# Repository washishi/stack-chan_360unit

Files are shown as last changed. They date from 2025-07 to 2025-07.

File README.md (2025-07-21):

# stack-chan_360unit
Rotation unit for Takao's SCS0009 version stack chan

## 説明
-  タカヲ([@mongonta555](https://x.com/mongonta555))さんの [SCS0009サーボ専用 ｽﾀｯｸﾁｬﾝ](https://raspberrypi.mongonta.com/about-products-stackchan-m5gobottom-version/) を回転させてもUSBケーブルが邪魔にならないようにするユニットです
- [【SCS0009専用】ｽﾀｯｸﾁｬﾝ タカオ版 ケースセット](https://mongonta.booth.pm/items/5186064)に後付けできます
-  M5Coreへの電源供給は Groveポート経由、USBコネクタ経由(外部/内部)いずれかで行うことができます  
-  USBコネクタ(外部/内部)を利用した場合は電源の供給だけでなくデータ通信も行うことができます
  
<br>
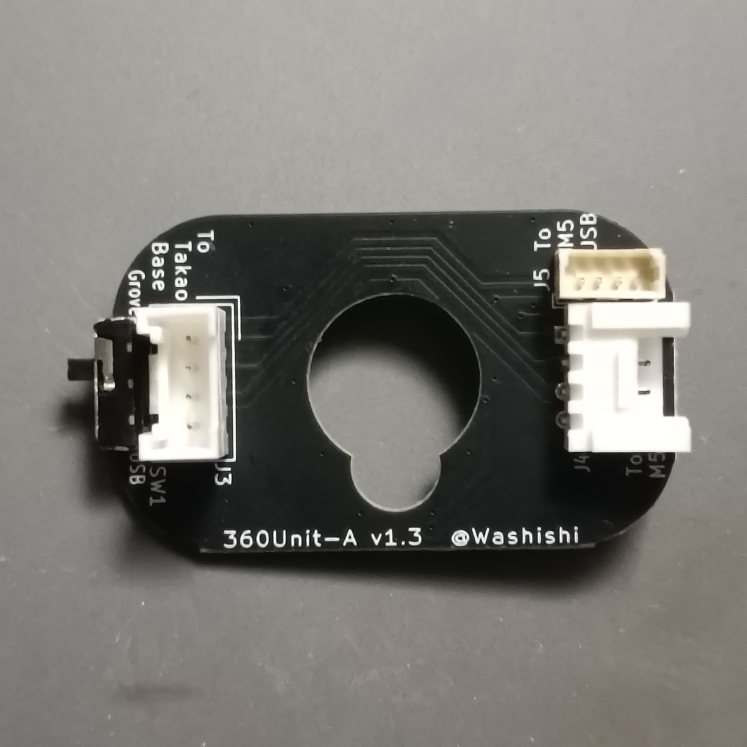
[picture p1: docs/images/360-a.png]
<br>

## BOOTHで頒布するセットの説明
BOOTHで頒布する[タカヲ版 SCS0009 ｽﾀｯｸﾁｬﾝ用 360ユニット セット](https://washishi.booth.pm/items/7204147)は下記のセットとなっています
<br>
1. 360ユニット 基板A  
   電源等を伝達するための基板です  
   GroveおよびUSB接続用のコネクタ、電源供給先切替用のスイッチが付いています
2. 360ユニット 基板B  
   電源元のUSBからの受電部です ここにACアダプタ等を接続します(同時に他の場所等の2か所から給電しないでください)  
   USB Type-C コネクタ部分は スーザン＠子育てエンジニア([@suzan_works](https://x.com/suzan_works)
)さんの  
[プリント基板製USB-Cコネクタ](https://suzan-works.booth.pm/items/6574802)の[設計データ](https://github.com/suzan-works/USB-C_PCB_Receptacle)を利用させてもらっています  
USB Type-Cコネクタを刺すため厚さは0.8mmです
3. サーボ用スペーサー
   360Unitの接点の入る厚みを確保するために足側のサーボとブラケットの間に挟みます
4. USB(外部)用ケーブル  
   M5CoreのUSB Type-C 端子と接続する場合に利用するケーブルです  
   LLMモジュールを付けている場合はそちらのUSB Type-C端子に接続することもできます  
   結線はCore内部の表記と同じで下記となります  
    1.+5V(赤)  
    2.GND(黒)  
    3.D-(DM) (黄)  
    4.D+(DP) (緑)  
5. USB(内部)用ケーブル  
   Core2 や CoreS3※,S3SE,S3Lite 等の内部にある1.25mmピッチのUSBコネクタと接続する場合に利用するケーブルです  
   コネクタ同士の結線はストレート(同じピン同士が接続)です  
   ※CoreS3の初期ロット？にはこのコネクタが実装されていない様です
6. Groveケーブル 10cm  
   GroveコネクタからM5Coreに給電する際に360ユニットとCoreのGrove端子を接続するケーブルです   
7. 1.25mmピッチコネクタ  
   CoreS3の初期ロット？では内部USBコネクタが未実装の様なので自分で実装する場合の為に1つ添付しています・・・がCoreS3の分解は難易度が高い為自信がない場合は行わない方がいいです(分解方法についてもここでは解説しません)
## 組み立て方
1. 利用する工具等
   - ドライバ　または 六角レンチ  
     ｽﾀｯｸﾁｬﾝの足(サーボホーン)とサーボの固定ネジの取り外し/取り付けに利用します  
     利用しているネジに合ったものを準備してください
   - やすり  
     サーボホーンがガタつくときや360ユニット基板Bがはめにくい場合に使う場合があります(100均のダイヤモンドやすりでかまいません)
   - ニッパー  
     サーボ用スペーサーを切って取り付ける場合は利用します
   - ピンセット  
     コネクタを刺す際にあると便利です

2. すでにｽﾀｯｸﾁｬﾝが組みあがっている場合は正面を向いた状態(サーボが中点)で停止します  
   新規で組み立てる場合も位置を動かしてしまっている場合は中点に合わせてください
3. ｽﾀｯｸﾁｬﾝの足(サーボホーン)のネジを外して取り外します  
   サーボホーンを乗せた状態でガタつかず水平になることを確認します  
   ガタつく場合はサーボホーンの側面(下記写真の赤色部分)を少しやすりで削って足の固定部分と干渉しないようにします  
     
4. 360ユニット 基板B を写真の向きで足にはめます  
   窪みに合わせてサーボホーンに当たるまで押し込みます  
   はめにくい場合は基板の側面をやすりで少し削ってください  
   
5. サーボの固定ネジ(2本)を取り外しサーボとブラケットの間にスペーサーを入れて再度固定ネジで止めます  
   組みあがった状態だとサーボのケーブルを一度外す必要があり面倒なので写真のようにスペーサーをニッパーでカットしてしまってもいいです  
 <br>
 <br>

6. 360ユニット 基板Aを写真の向きでサーボにはめてからｽﾀｯｸﾁｬﾝの足を再度取り付けます  
<br>
※足をねじ止めする前に次の「7.配線」を行った方が配線がしやすいかもしれません

7. 配線  
   コネクタ同士の配線を行います

   以下の接続ができます  
   - USB(外部)給電 (CoreのUSBコネクタから給電)
   - USB(内部)給電 (Core2,S3系(※)の内部USBコネクタから給電) 
   - Grove給電 (CoreやGoBottomのGroveポートから給電)  
    
    接続方法  
      |給電|接続方法|スイッチ|データ  通信|  
    |:-|:--|:--|:-:| 
    |USB<br>(外部)|「To M5 USB」と M5Core のUSBコネクタを「USB(外部)用ケーブル」で繋ぎます|USB側|可|  
    |USB<br>(内部)|「To M5 USB」と M5Core2,S3系(※)の内部USBコネクタを「USB(内部)用ケーブル」で繋ぎます|USB側|可|  
    |Grove|M5CoreやGOBottomのGroveポートを「GROVEケーブル」で「To M5」のGroveポート(横)と繋ぎます、TakaoBASEは「To TakaoBase」のGroveポート(縦)に繋ぎます|Grove側|不可|  

   - USBとGroveの両方の配線を行っても電源の供給先はスイッチで切替となるので問題ありません  
   - ※CoreS3の初期ロット？では内部USBコネクタが実装されていません(使う場合はCoreS3を分解して自分で実装する必要があります)  
  
USB(内部)コネクタ(左写真)、USB(内部)コネクタ利用でLLMモジュールを付ける場合はLLMモジュールの基板下に少し隙間があるので一度基板を止めているネジを外して通してください(右写真)  


配線の完了で作業は完了です  

## 使い方
ｽﾀｯｸﾁｬﾝの足の後ろに飛び出しているUSB Type-CコネクタにACアダプタやPCを接続して給電します  
CoreとUSBケーブル(外部/内部)で接続している場合はPCと繋ぐとプログラム書き込み等のデータ通信も行えます  


## 基板制作データ等
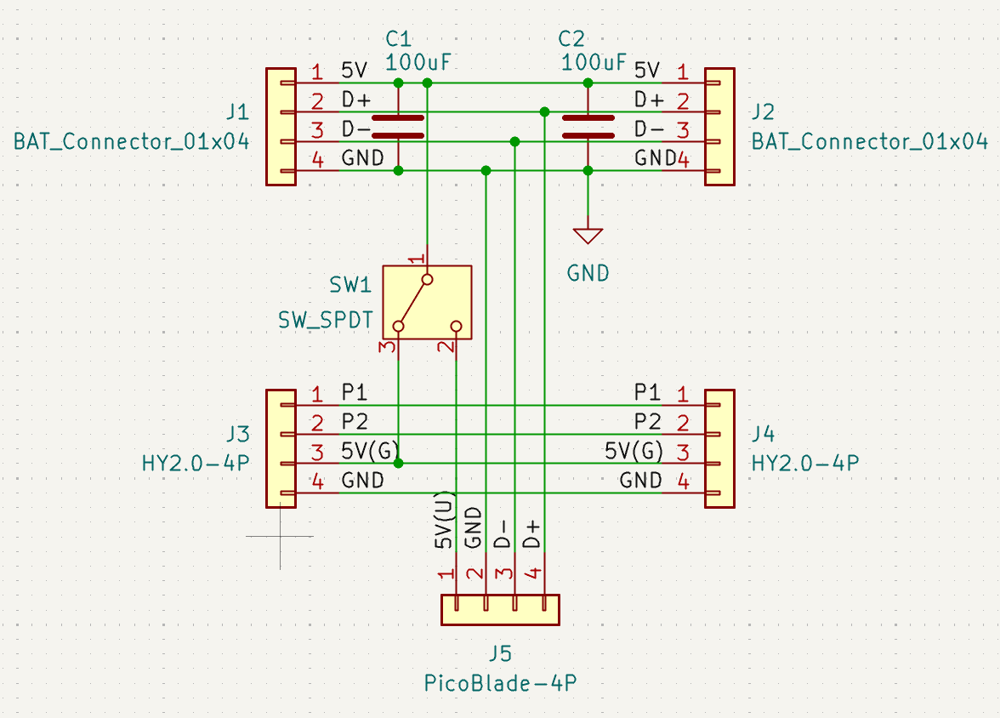
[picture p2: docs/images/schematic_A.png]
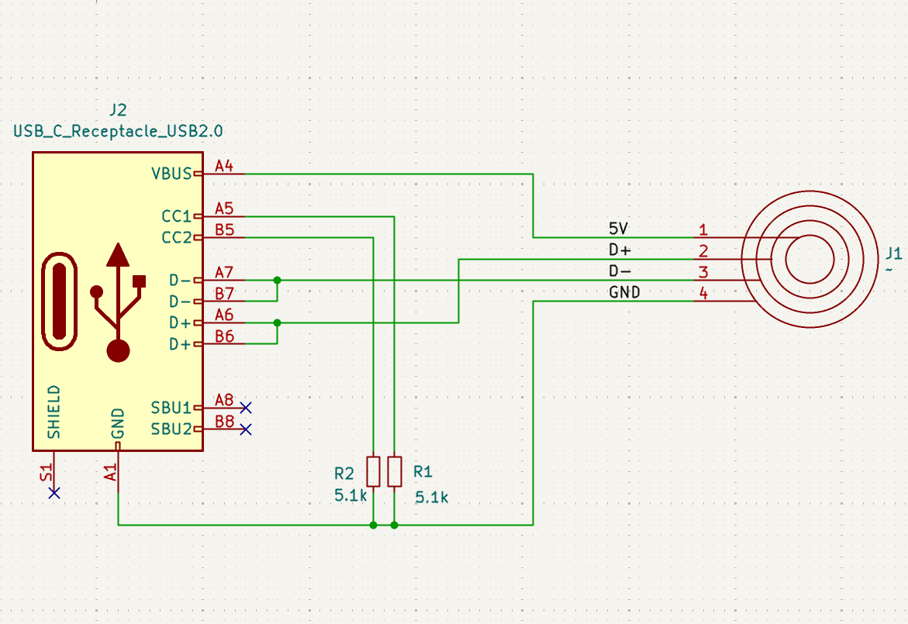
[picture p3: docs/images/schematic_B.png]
<br>
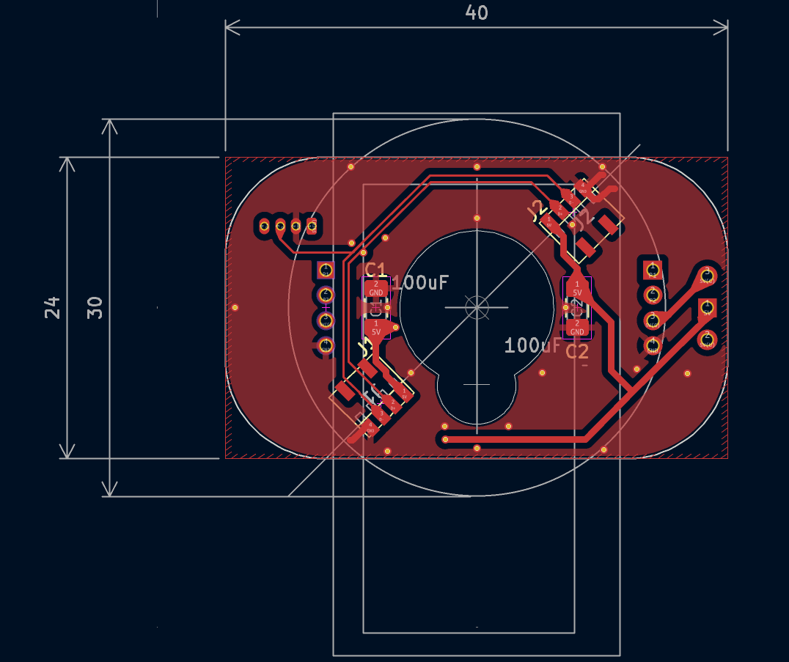
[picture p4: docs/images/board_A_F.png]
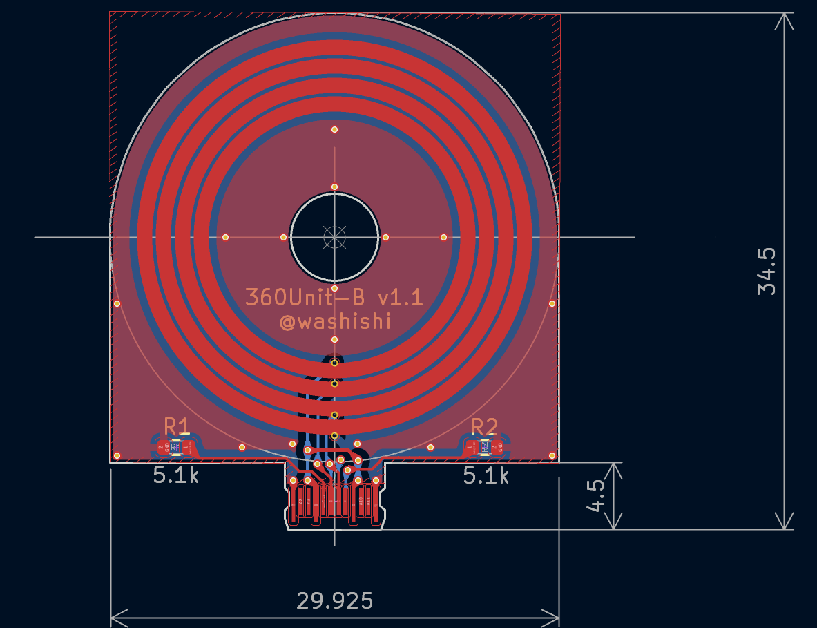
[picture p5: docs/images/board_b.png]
<br>

本リポジトリ schematics の配下に kicad (v9)で作成した回路図、基板データ一式があります  
また schematics/production 配下には基板発注に利用するガーバデータのzipファイルもあります

## BOM(部品リスト)
|名称|仕様|メーカー|個数|備考|備考購入先|  
|:--|:--|:-:|:-:|:--|:--|
|基板|stack-chan 360Unit A基板|-|1||[JLCPCB](https://jlcpcb.com/JPV)へ発注|
|基板|stack-chan 360Unit B基板|-|1|厚さ0.8mm|[JLCPCB](https://jlcpcb.com/JPV)へ発注|
|チップ抵抗|5.1KΩ 1608サイズ|-|2||[秋月電子](https://akizukidenshi.com/catalog/g/g130338/)100個セット|
|チップ積層セラミックコンデンサ|100uF 10V 3216サイズ|-|1||[秋月電子](https://akizukidenshi.com/catalog/g/g115633/)10個セット|
|スイッチ|2.5mmピッチ SPDT サイド型|-|1||[秋月電子](https://akizukidenshi.com/catalog/g/g115370/)|
|Groveコネクタ|HY2.0-4P ストレート|-|1||[秋月電子](https://akizukidenshi.com/catalog/g/g131074/)10個セット|
|Groveコネクタ|HY2.0-4P L形|-|1||[秋月電子](https://akizukidenshi.com/catalog/g/g112634/)10個セット|
|1.25mmコネクタ ケーブルセット|4P 10cm 片側のみコネクタ圧着|-|2|ケーブル1<br> コネクタ2|[Aliexpress](https://ja.aliexpress.com/item/1005006003135511.html)10ペア セット||
|1.25mmコネクタ ケーブル|4P ストレート 100mm<br>両側コネクタ|-|1||[Aliexpress](https://ja.aliexpress.com/item/1005005898168919.html)10個セット||
|USB Type-Cコネクタ|MX-12とあるもの|-|1||[Aliexpress](https://ja.aliexpress.com/item/1005007581371610.html)||
|バッテリー端子|smd 1.27mmピッチ 4P|-|2|ばね接点|[Aliexpress](https://ja.aliexpress.com/item/1005005302903409.html)5個セット||
|シリコンチューブ|内径2mm外形3mm|-|6cmほど|USB(外部)ケーブルに被せてます|[Aliexpress](https://ja.aliexpress.com/item/1005001499980646.html)1m||

## 3Dモデル等
3D_Model 配下に 下記の利用した3Dモデルデータ(STEP,STL形式)があります
 - サーボスペーサ
 - USB Type-C コネクタケース 上部
 - USB Type-C コネクタケース 下部

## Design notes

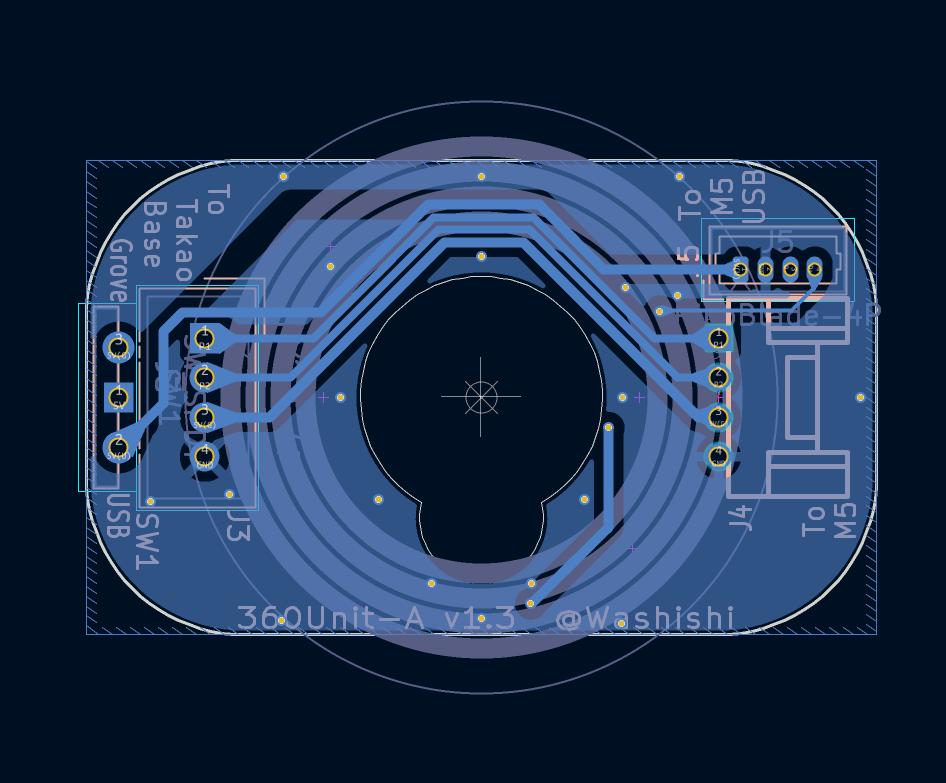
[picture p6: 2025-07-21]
docs/images/board_A_B.png

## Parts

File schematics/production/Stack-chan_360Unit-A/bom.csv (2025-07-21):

Designator | Footprint | Quantity | Value | LCSC Part #
C1, C2 | 1206 | 2 | 100uF
J1, J2 | BatteryConector_1.27mm_4P | 2 | BAT_Connector_01x04
J3 | NS-Tech_Grove_1x04_P2mm_Vertical | 1 | HY2.0-4P
J4 | CON_GROVE_H | 1 | HY2.0-4P
J5 | Molex_PicoBlade_53047-0410_1x04_P1.25mm_Vertical | 1 | PicoBlade-4P
SW1 | SW_Slide-03_Wuerth-WS-SLTV_9x3.5x3.5_P2.54mm | 1 | SW_SPDT

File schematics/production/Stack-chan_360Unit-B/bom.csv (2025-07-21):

Designator | Footprint | Quantity | Value | LCSC Part #
J1 | RingTerminal | 1 | ~
J2 | USB-C_PCBPLUG | 1 | USB_C_Receptacle_USB2.0
R1, R2 | 0603 | 2 | 5.1k

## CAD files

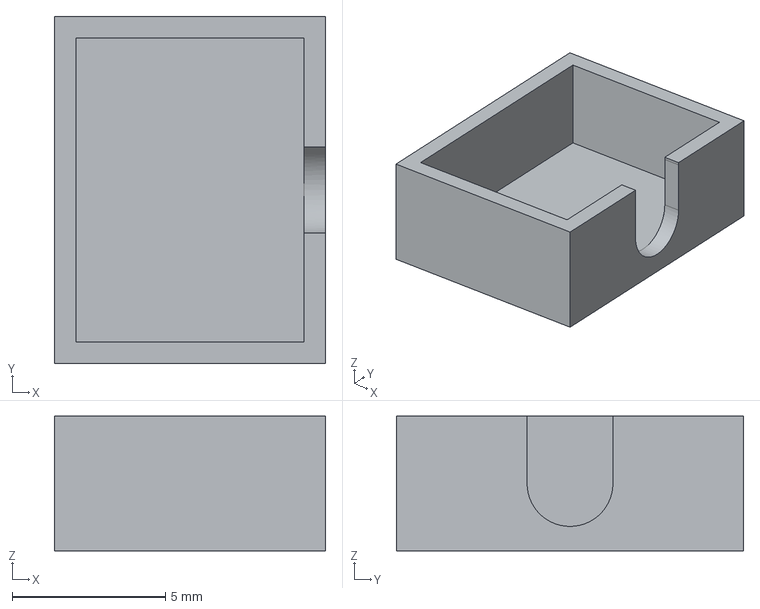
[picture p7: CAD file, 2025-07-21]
3D_Model/USB-C_Top.step
8.85 x 11.3 x 4.40 mm

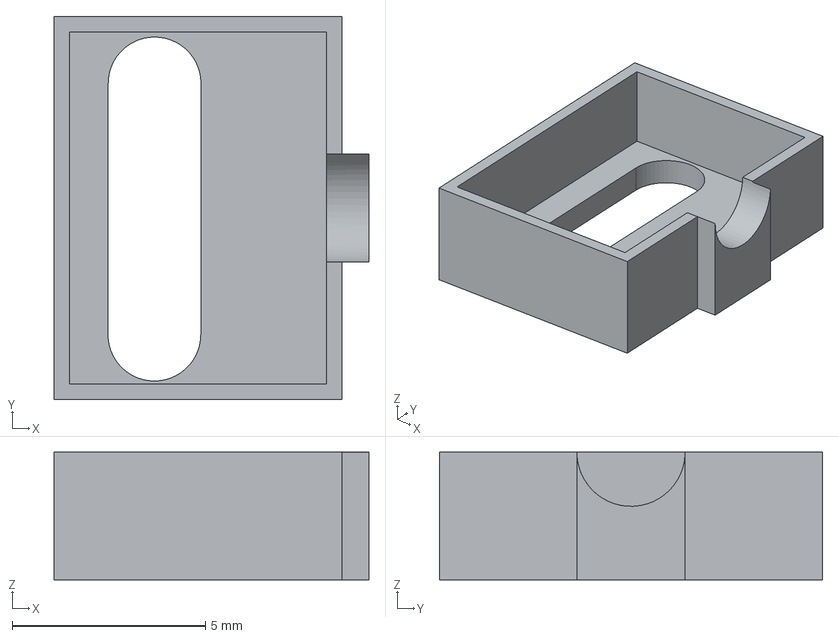
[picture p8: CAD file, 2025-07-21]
3D_Model/USB-C_Bottom.step
8.15 x 9.92 x 3.30 mm

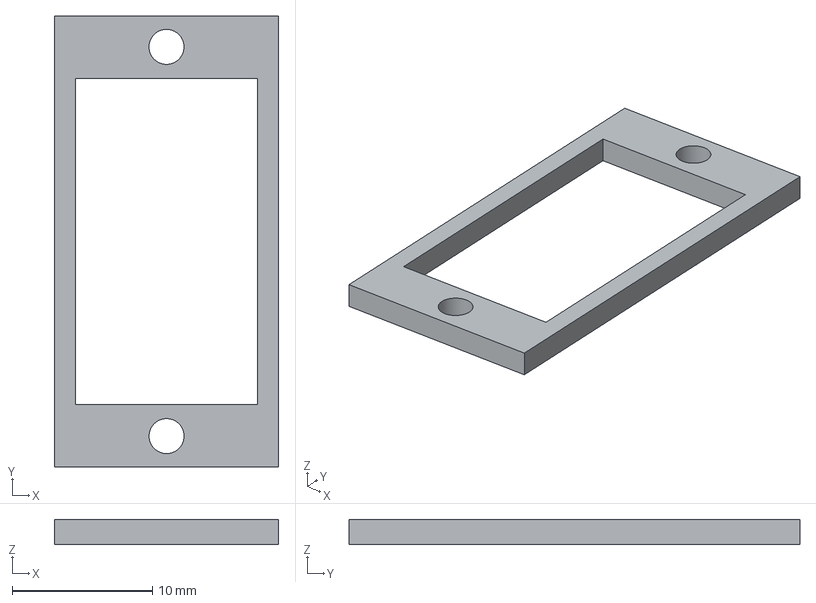
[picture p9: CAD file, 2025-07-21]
3D_Model/Servo_Spacer.step
16.0 x 32.2 x 1.80 mm

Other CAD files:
3D_Model/Servo_Spacer.stl
3D_Model/USB-C_Bottom.stl
3D_Model/USB-C_Top.stl

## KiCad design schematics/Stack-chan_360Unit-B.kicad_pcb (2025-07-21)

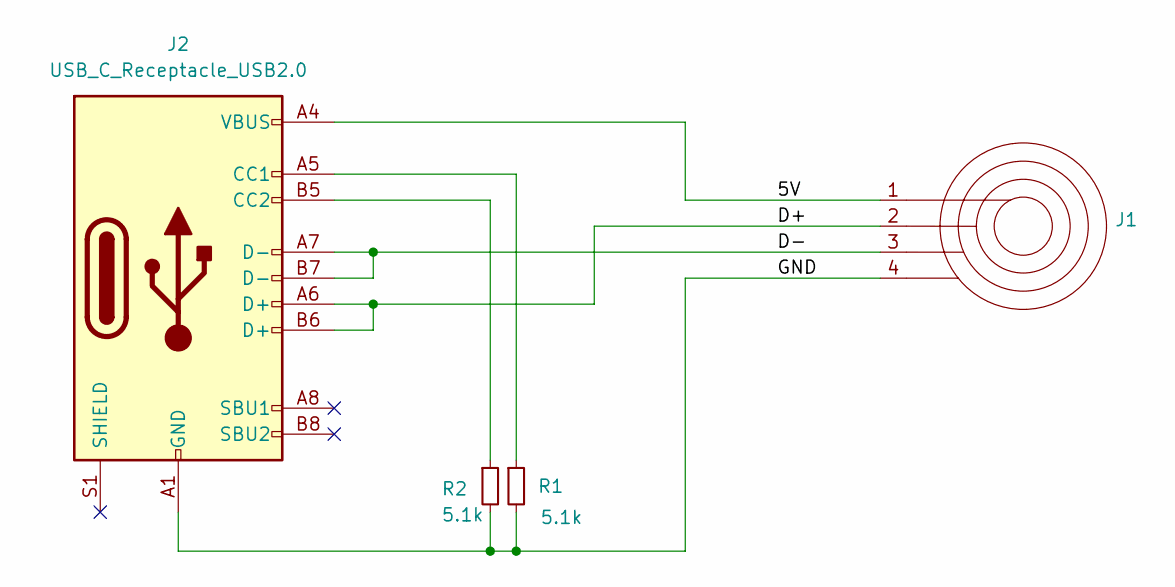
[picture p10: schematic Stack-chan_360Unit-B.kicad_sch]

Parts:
J1: RingTerminal
J2: USB_C_Receptacle_USB2.0; USB-C_PCBPLUG
R1, R2: 5.1k; R_0603_1608Metric

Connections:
/5V: J1.1, J2.A4 (VBUS), J2.A9 (VBUS), J2.B4 (VBUS), J2.B9 (VBUS)
/D+: J1.2, J2.A6 (D+), J2.B6 (D+)
/D-: J1.3, J2.A7 (D-), J2.B7 (D-)
/GND: J1.4, J2.A1 (GND), J2.A12 (GND), J2.B1 (GND), J2.B12 (GND), R1.2, R2.2
unnamed: J2.A5 (CC1), R1.1
unnamed: J2.B5 (CC2), R2.1

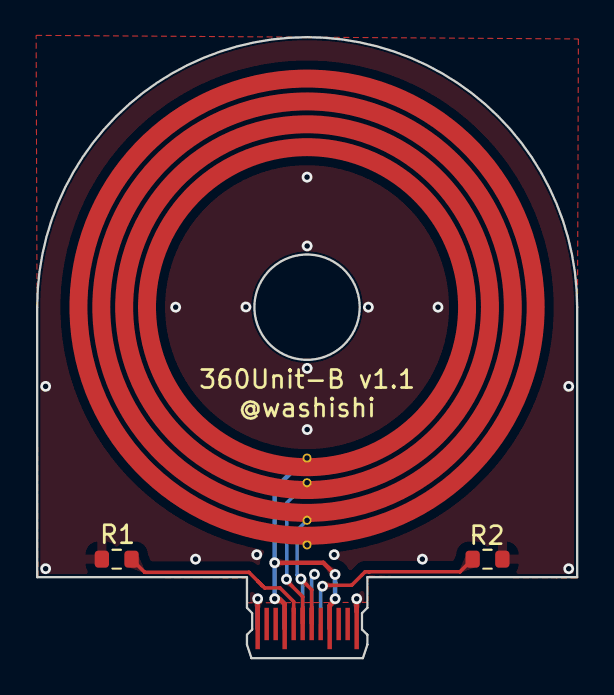
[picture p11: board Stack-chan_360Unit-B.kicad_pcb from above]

Board: 2 copper layers, 30.0 x 34.5 mm, 4 parts (0 on the bottom side), 6 nets.

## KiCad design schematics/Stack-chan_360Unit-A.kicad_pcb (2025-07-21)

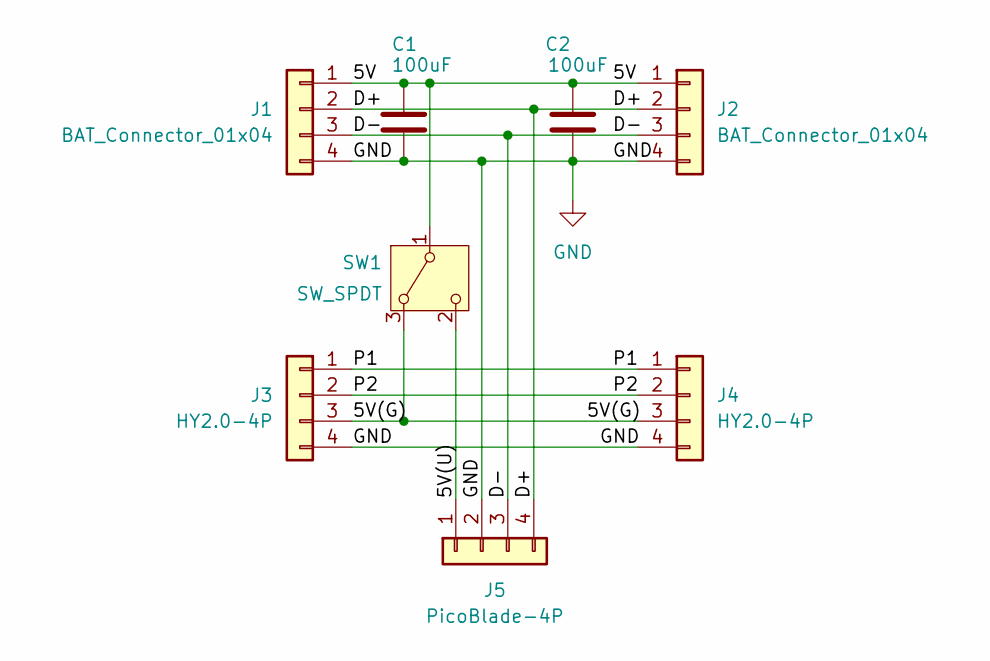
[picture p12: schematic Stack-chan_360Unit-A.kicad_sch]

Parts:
C1, C2: 100uF; C_1206_3216Metric_Pad1.33x1.80mm_HandSolder
J1, J2: BAT_Connector_01x04; BatteryConector_1.27mm_4P
J3: HY2.0-4P; NS-Tech_Grove_1x04_P2mm_Vertical
J4: HY2.0-4P; CON_GROVE_H
J5: PicoBlade-4P; Molex_PicoBlade_53047-0410_1x04_P1.25mm_Vertical
SW1: SW_SPDT; SW_Slide-03_Wuerth-WS-SLTV_9x3.5x3.5_P2.54mm

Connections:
/5V: C1.1, C2.1, J1.1, J2.1, SW1.1 (B)
/5V(G): J3.3, J4.3, SW1.3 (A)
/5V(U): J5.1, SW1.2 (C)
/D+: J1.2, J2.2, J5.4
/D-: J1.3, J2.3, J5.3
/P1: J3.1, J4.1
/P2: J3.2, J4.2
GND: C1.2, C2.2, J1.4, J2.4, J3.4, J4.4, J5.2

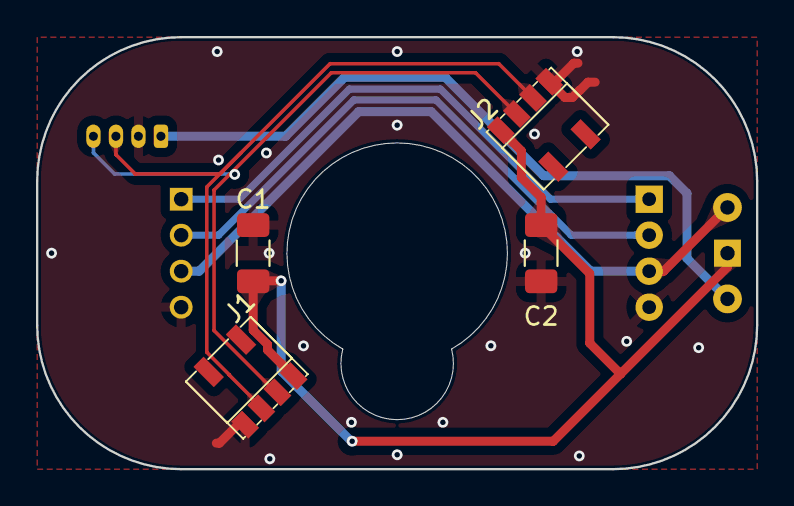
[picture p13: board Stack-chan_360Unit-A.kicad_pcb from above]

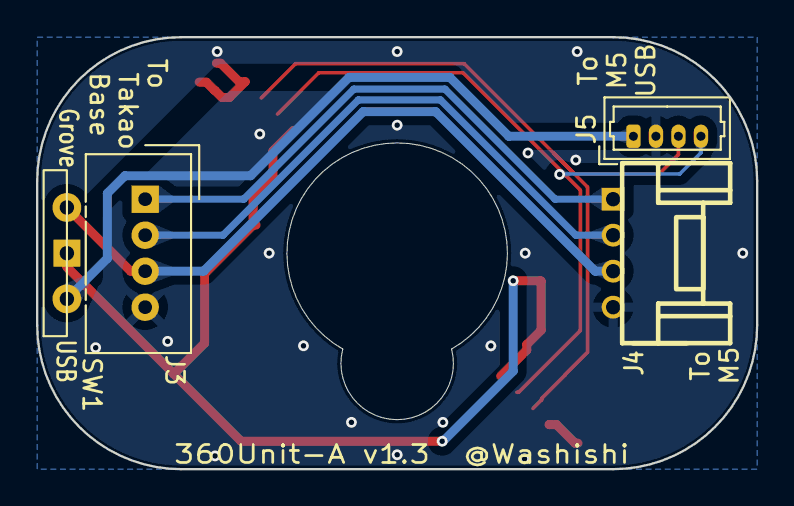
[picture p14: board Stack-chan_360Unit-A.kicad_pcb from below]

Board: 2 copper layers, 40.0 x 24.0 mm, 8 parts (4 on the bottom side), 8 nets.
